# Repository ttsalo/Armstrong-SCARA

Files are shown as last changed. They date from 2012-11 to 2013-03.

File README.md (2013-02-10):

Armstrong, the parallel SCARA 3D printer.

Current version is the A1. It's already capable of printing actual
objects, but is very much in the prototype/alpha stage.

NOTE! The STL files may be out of date at any given time. If you want to
reproduce this, use the SCAD files instead.

Concise contruction instructions:

1. Print plastic parts. You need:
 1 x arm11
 1 x arm12
 1 x arm22
 1 x arm21
 1 x z-carriage
 1 x z-end-bottom
 1 x z-end-top
 1 x z-end-support
 2 x circspline-spline
 2 x circspline-motor-mount
 2 x flexspline
 2 x wave-rotor
 4 x mendel-rod-clamp (from Prusa 2, not included here)
 1 x mendel-coupling (from Prusa 2, the Z rod to motor coupling, not included)

 Everything else except the flexsplines should print fine with 0.25 or 0.3 mm
 layer height. The flexspline should be printed with 0.2 layer height, 2.0
 W/T parameter, one perimeter, no extra perimeters. Retract minimum length
 should be set to 1 mm to force retraction when infilling the teeth. Slic3r
 normally does full infill for the teeth regardless of the infill solidity,
 this is fine.

2. Assemble the arms.
  2.1. Left arm, middle joint, from top down: M8x50 bolt, washer, 608
       bearing, arm11, 608 bearing, washer, arm21, washer, locking nut.
  2.2. Right arm, middle joint, from top down: M8x50 bolt, washer, arm22,
       washer, 608 bearing, arm12, 608 bearing, washer, locking nut.
  2.3. Final (end effector) joint, three times: M4x20 hex key bolt, 
       arm21, 4xwasher, 624 bearing, washer, nut. The 624 bearings should
       run smoothly in the groove of the arm22.

3. Mount arms onto the z-carriage.
  3.1. For each: M8x50 bolt, washer, 608 bearing, flexspline, arm11 or arm12,
       608 bearing, washer, z-carriage, washer, locking nut.

4. Tighten the nuts so that there is no play but the arms move without effort.

5. Insert six M4 nuts in the nut traps of the z-carriage.

6. Place the circsplines on top of the z-carriage (may require some fiddling
   or forcing into place) and check that they mesh with the flexsplines.

7. Mount NEMA17 motors in the motor mounts using M3x8 conical head (sunken)
   screws.

8. Assemble wave drivers. In each end: M4x20 bolt, washer, wave-driver,
   washer, 624 bearing, washer, wave-driver other screw hole, washer,
   locking nut. The wave driver length is critical. The included STLs
   have 52.75 mm total outside dimension. This should work fine at least
   initially. When the drives have been run for some time, wave drivers
   with larger dimensions may be needed (in 0.25 mm increments) to get
   rid of backlash. The drivers are for motors with 20 mm shafts with
   double flats. Other types of motors may need redesigned drivers.

9. Assemble the motor mounts into the z-carriage, 6xM4x20 bolts and washers
   are needed. The wave drivers should insert nicely into the flexsplines
   when the motors are rotated a bit by hand when inserting them.

10. Insert 4xLM8UU linear bearings into the z-carriage, use M3x20 screws
    and nuts for each.

11. Construct the frame. Anything L-shaped and at least 80 mm wide will do.
    Just mount the z-end parts with M8 bolts. If the L-part is sufficiently
    supported, the z-end-support part may be omitted. The height can be
    freely chosen.

12. Mount the 8 mm smooth rods with the bar clamps and M3x24 bolts, nuts
    and washers. Place the z-carriage at the same time and check that it
    travels freely on the rods.

13. Insert a M8 nut into the z-carriage and screw in a M8 threaded rod
    for the Z travel.

14. Mount the Z motor with M3x8 sunken head screws and attach it to the
    M8 threaded rod with the coupling.

15. Place the print bed in the frame. The print area is 200x120, with the
    nearest Y position being 82 mm from the centerline of the arm base
    joints.

16. Mount the extruder. The arms will accept a groove mount extruder
    with small diameter. Tested with J-Head Mk V-b. The mounting bolts
    have the standard 50 mm pattern. (M4 bolts)

17. Do the electrical connections and upload the Marlin SCARA firmware.

18. The printer should now be ready for use.

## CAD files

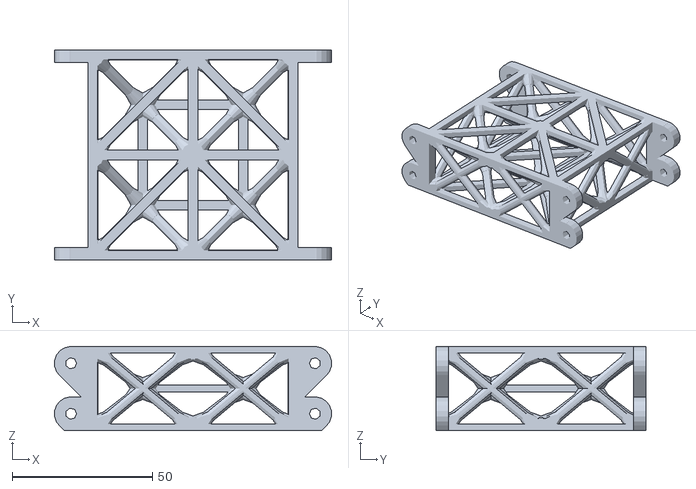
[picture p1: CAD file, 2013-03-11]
frame-bed.stl
98.8 x 75.0 x 30.0

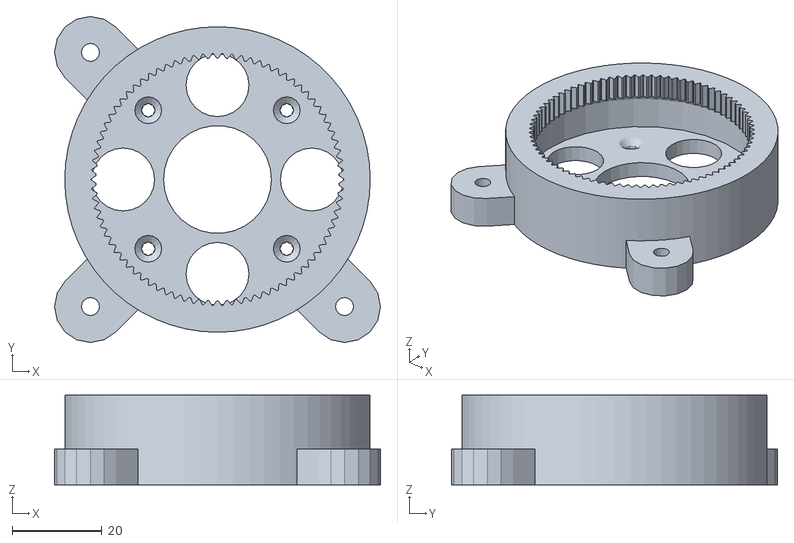
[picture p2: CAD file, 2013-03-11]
circspline.stl
72.6 x 72.6 x 20.0

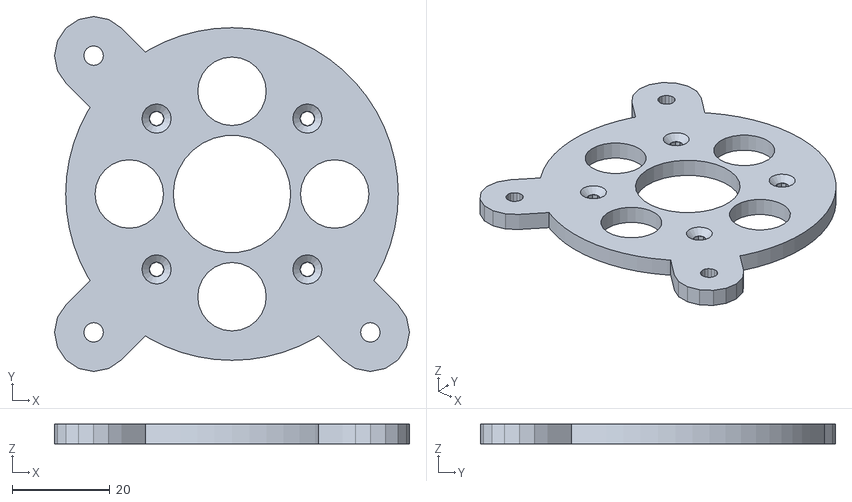
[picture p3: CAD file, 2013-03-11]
circspline-motor-mount.stl
72.6 x 72.6 x 4.00

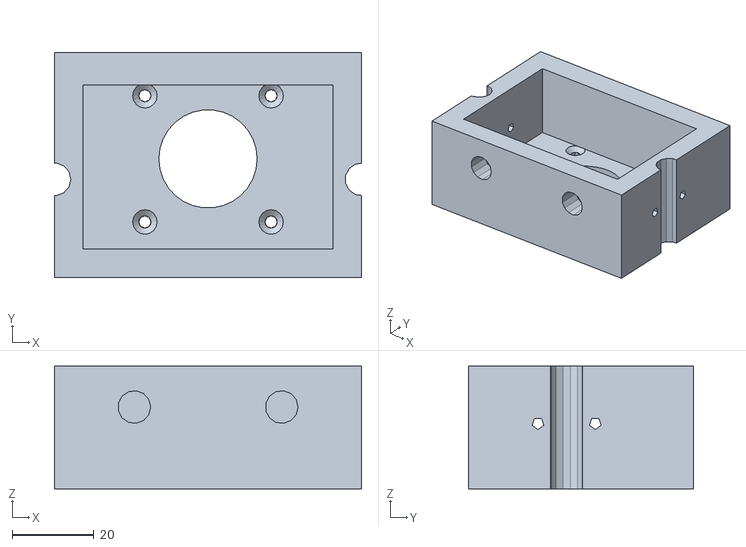
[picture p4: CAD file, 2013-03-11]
z-end-top.stl
75.0 x 55.0 x 30.0

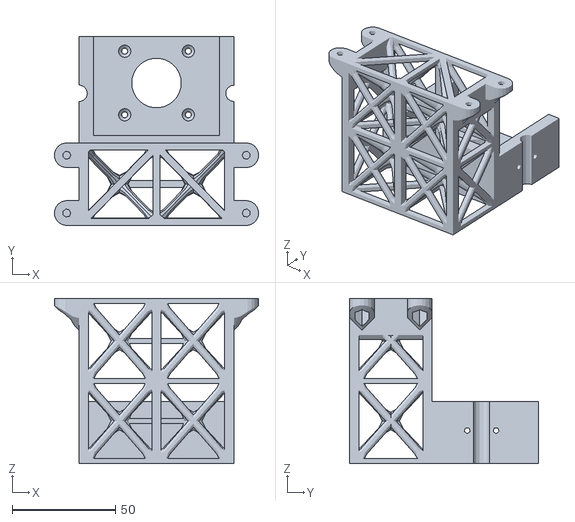
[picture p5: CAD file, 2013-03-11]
frame-top.stl
98.8 x 91.5 x 80.0

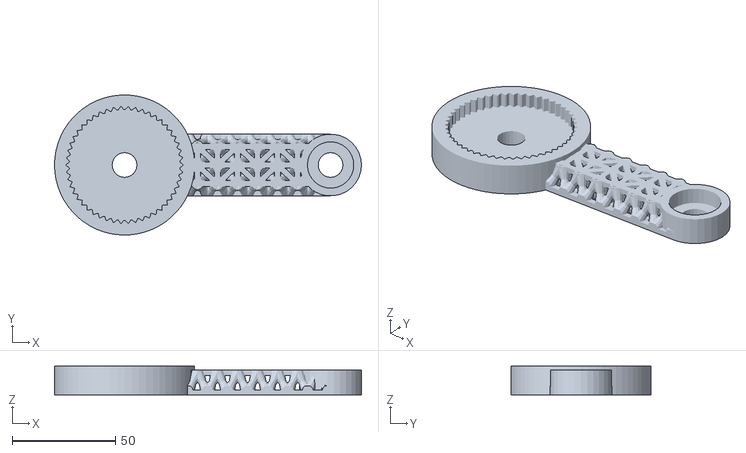
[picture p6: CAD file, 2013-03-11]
arm11.stl
149.0 x 68.0 x 14.0

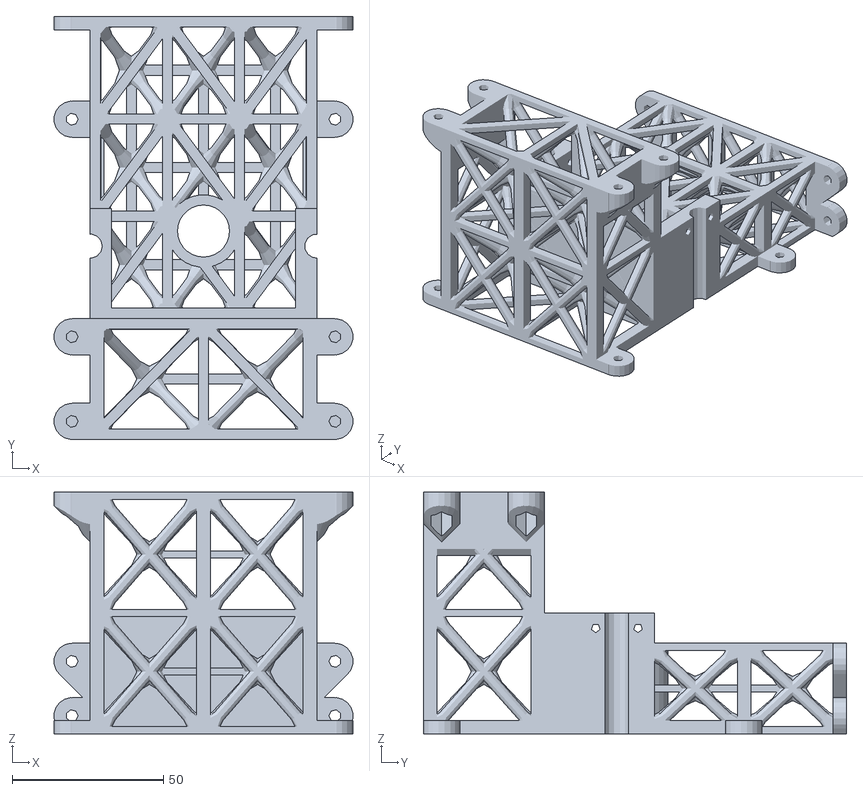
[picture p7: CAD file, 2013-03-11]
frame-bottom.stl
98.8 x 140.0 x 80.0

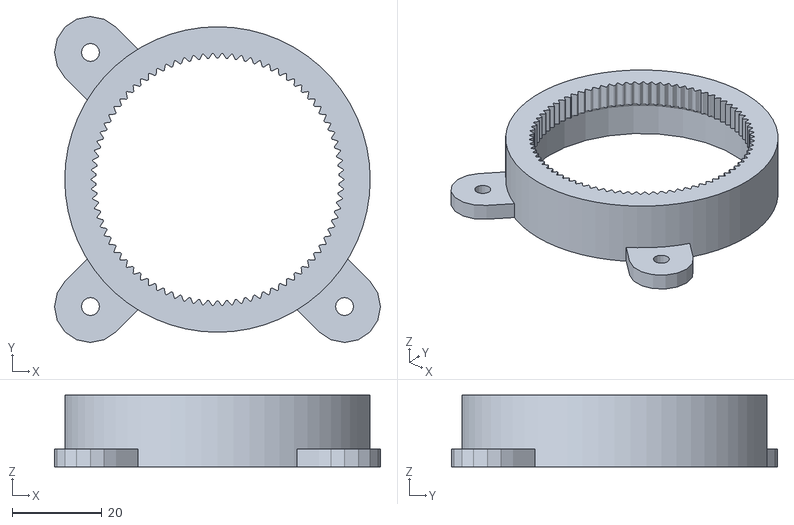
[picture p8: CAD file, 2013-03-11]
circspline-spline.stl
72.6 x 72.6 x 16.0

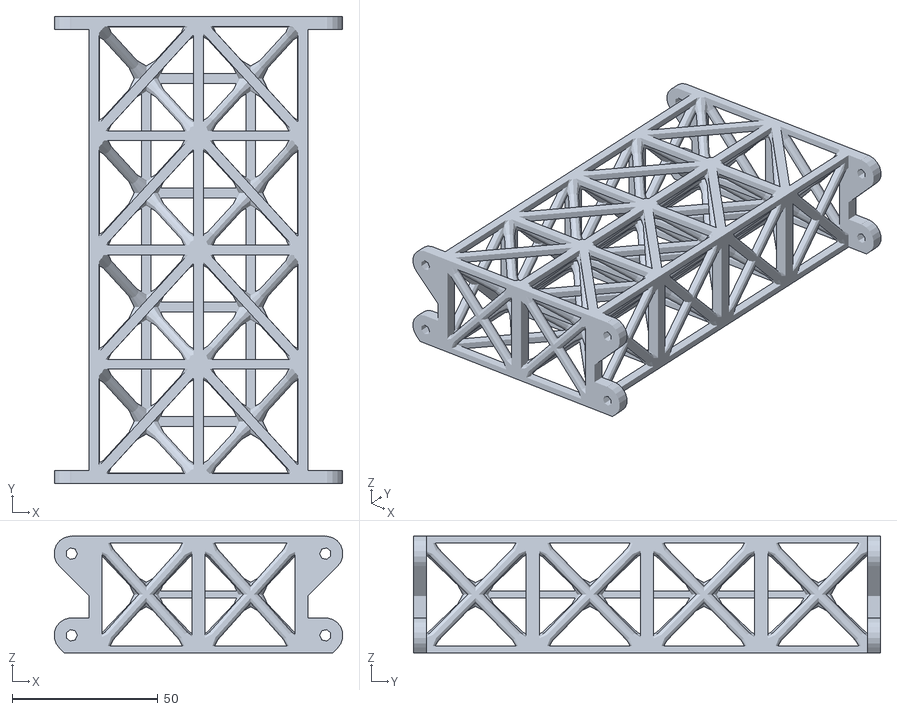
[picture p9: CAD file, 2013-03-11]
frame-extension-double.stl
98.8 x 160.0 x 40.0

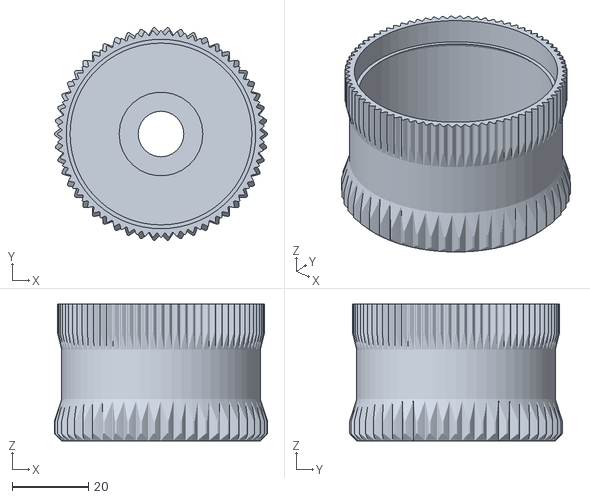
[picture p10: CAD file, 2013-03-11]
flexspline.stl
56.0 x 55.9 x 36.0

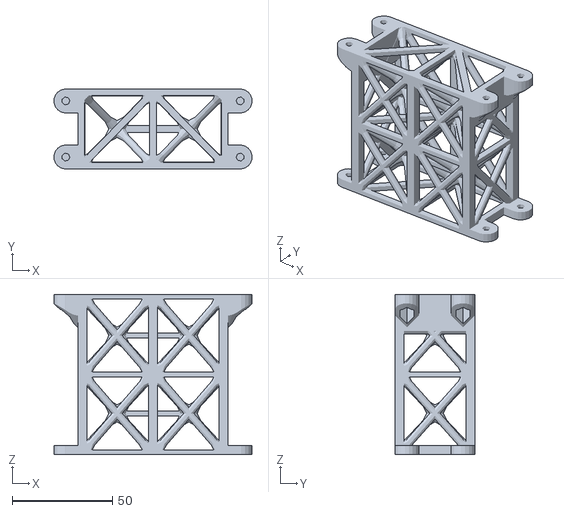
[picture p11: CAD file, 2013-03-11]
frame-extension.stl
98.8 x 40.0 x 80.0

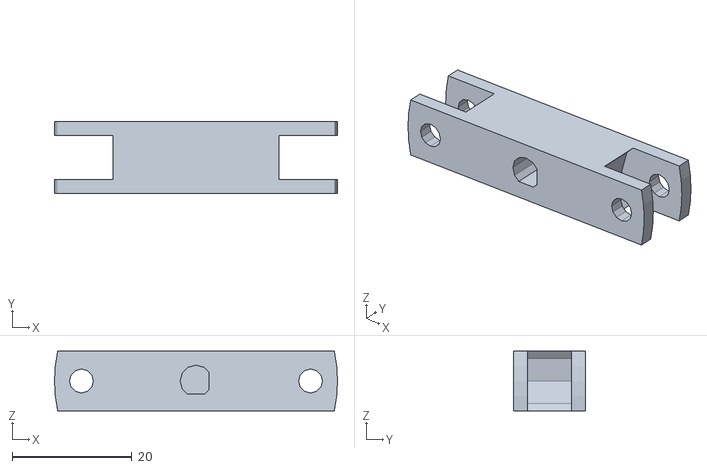
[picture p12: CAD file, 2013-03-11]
wave-rotor.stl
47.2 x 12.0 x 10.0

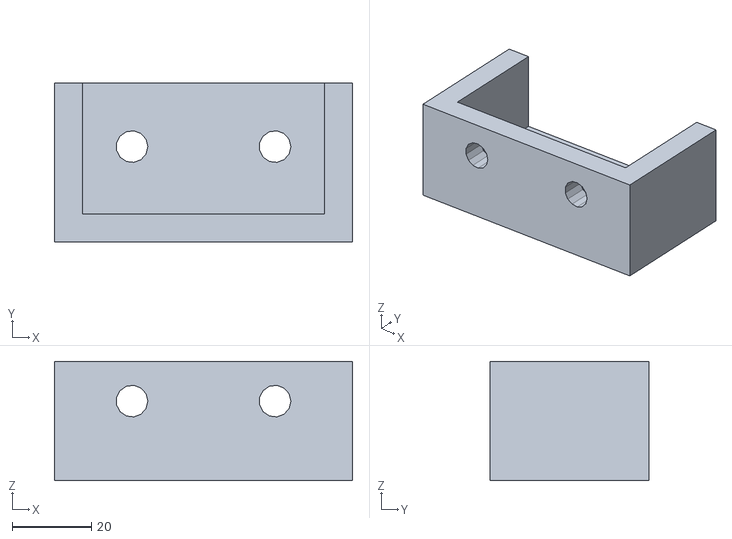
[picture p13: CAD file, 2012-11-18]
z-end-support.stl
75.0 x 40.0 x 30.0

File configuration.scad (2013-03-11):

// Harmonic drive main parameters
press_angle = 35;
flex_teeth = 80;
teeth_diff = 2;

tol = 0.25; // generic tolerance used in some places
lh = 0.3; // layer height needed in a few places

// Main geometry
bearing_r = 22/2;
bearing_h = 7;
washer_h = 1;
bolthead_h = 4;
stepper_shaft_h = 20;
circ_drive_bearing_indent = 1;
flex_bearing_indent = 1;
drive_bearing_r = 13/2;
drive_bearing_h = 7;

// Flexspline dimensions
flex_inner_r = 25.3;
flex_outer_r = 27.6; // was 27.3; // Outer radius clips the teeth peaks, if needed.
flex_h = 36;
flex_bottom_h = 2;
flex_bolthole_r = 6;
flex_bottom_tooth_h = 3; // The height of the straigth part of the bottom teeth
flex_upper_slope_h = 6; // Length of slope from straight part to upper teeth
flex_wt = 0.81; // Wall thickness of the straigt part
flex_extra_upper_wt = 0.4; // Extra wall thickness for the inside of the upper toothed part
flex_lip = 1.4; // Wave driver retaining lip thickness
pitch = 120.5; // Tooth pitch. Tune this to make the tooth valleys line up with the
               // outer surface.
helix_twist = 0; // 3.5;
flex_bottom_teeth = 50;
flex_bottom_pitch = 197;
bottom_press_angle = 40;

// Circspline dimensions
circ_h = 20;
circ_outer_r = 34;
circ_inner_r = 30;
circ_bottom_h = 4;
// Negative clearance cuts a bit from the top of the teeth
circ_tooth_clearance = -0.25;

// Wave driver dimensions
wave_radius = 51.25/2;
driver_h = 12;
driver_w = 10;
driver_tol = 0.15;
drive_bearing_spacing_r = wave_radius - drive_bearing_r;

// The total height of the drive unit, excluding the motor and flexspline base.
assy_h = 50;
stepper_shaft_l = 20;

tooth_overlap = (flex_h + circ_h) - assy_h;

// Position of the middle of the tooth overlap section on the stepper shaft.
stepper_shaft_mid_rot = circ_h - tooth_overlap/2;

echo(str("Tooth overlap: ", tooth_overlap));
echo(str("Drive midpoint on stepper shaft: ", stepper_shaft_mid_rot));

red_r = teeth_diff/flex_teeth;
echo(str("Reduction ratio: 1/", flex_teeth/teeth_diff, " (", red_r, ")"));
echo(str("With 200x16 motor, arc minutes per microstep: ", 360*60/(200*16)*red_r));
echo(str("Linear resolution (mm) for 100 mm arm: ", sin(360/(200*16)*red_r) * 100));
echo(str("Torque (N) at 100 mm for 40 Ncm motor: ", 4/red_r));
echo(str("Linear speed equivalent to standard Prusa's 300 mm/s at 100 mm: ",
         300*80 * sin(360/(200*16)*red_r) * 100));

// Circspline mount dimensions
circ_mount_r = circ_outer_r + 6;
circ_mount_h = 8;
circ_mount_1 = 45;
circ_mount_2 = 135;
circ_mount_3 = 225;

// Master arm height setting
main_arm1_height = 12;
main_arm2_height = 12;

// Arm 1st segment dimensions
arm_flex_base_bottom_h = 8;
arm_flex_base_h = 14;
arm_joint1_base_h = main_arm1_height;
arm_joint1_base_r = 15;
arm_joint1_bearing_indent = 7;
arm_large_bolthole_r=6;
arm_w = 30;
arm1_h = main_arm1_height;

// default length
length = 100;

// New style truss details
truss_z_thickness = 2.5;
truss_xy_thickness = 3.4*(0.25/0.3);
truss_k_thickness = 3.4*(0.25/0.3);
truss_bar_diameter = 3.9*(0.25/0.3);

carr_truss_bar_diameter = 3.25;
carr_truss_thickness = 5;
carr_truss_width_coeff = 0.75;
carr_truss_radius = 0.1;

// Arm 2nd segment dimensions
arm2_h = main_arm2_height;
arm_separation = arm_joint1_base_h - arm_joint1_bearing_indent 
  + bearing_h + washer_h * 2;
arm_bolthole_r=4;
arm_joint2_base_h = main_arm2_height;
arm_joint2_base_r = 15;
arm_joint3_hollow_r = 10;
arm_joint31_base_h = main_arm2_height;
arm_joint31_base_r = 15;
arm_joint31_bearing_r = 13/2;
arm_joint31_bearing_h = 5;
arm_joint31_bearing_clearance = 2;
arm_joint32_base_h = main_arm2_height;
arm_joint32_base_r = 15;
arm_joint32_tube_h_clearance = 1;
arm_joint32_tube_wt = 2;
arm_joint32_tube_groove_depth = 1;
arm_joint31_bearing_spacing = arm_joint3_hollow_r + arm_joint32_tube_wt 
  + arm_joint31_bearing_r;

echo(str("Arm final stage vertical separation: ", arm_separation));
echo(str("Arm final stage total height: ", arm_separation + 2 * arm2_h));

// Default arm lengths
arm1_length = 100;
arm2_length = 150;
arm_spacing = 75;
arm_base_maxrot = 90 - asin((circ_outer_r + arm_w/2) / arm_spacing);
arm_joint_maxrot = 150; // hand-tuned
echo(str("Arm base minimum rotation to clear other base: ", arm_base_maxrot));

// Z carriage dimensions
carr_floor = 1; // Carriage floor thickness.
carr_wt = 3.5; // Carriage wall thickness.
carr_truss_width = arm_spacing + bearing_r * 2 + 20; // 120;
carr_truss_depth = 15;
drive_h = assy_h + bearing_h + washer_h 
  + arm_flex_base_bottom_h; // Total length needed by the drive unit.
carr_truss_length = circ_outer_r + 1 + carr_wt + bearing_r + 10;
carr_rod_offset = -46;
carr_drive_offset = -41;
carr_top_support_thickness = 3;
carr_top_support_width = 14;
carr_top_support_length = 70;

// Z end dimensions
z_end_bottom_thickness = 7;
z_end_bottom_width = arm_spacing + 20;
z_end_bottom_length = 40;
z_end_top_length = 55;
z_end_top_thickness = 7;
z_end_bottom_height = 30;
z_end_top_height = 30;
z_end_rod_offset = 24; // rod center from vertical plate

// Printable area and bed
print_ymin = 82; // Y=0 offset from arm bases (verify by simulation, see demo.scad)
print_xmax = 200;
print_ymin_frame_offset = -carr_rod_offset + z_end_rod_offset + print_ymin;
bed_bolt_r = 2;
bed_bolts = [[100-170/2, 100-124/2, 0], [100-170/2, 100+124/2, 0], [100+170/2, 100, 0]];

echo(str("Print area Y=0 offset from vertical frame: ", print_ymin_frame_offset));

// Frame dimensions
frame_bottom_height = 30;
frame_bottom_length = 100;
frame_back_height = 80;
frame_top_height = 80;
frame_extend_height = 80;
frame_back_depth = 40;
frame_back_width = arm_spacing;

frame_bottom_truss_z_thickness = 2.4;
frame_bottom_truss_xy_thickness = 3.4;
frame_bottom_truss_k_thickness = 3.4;
frame_bottom_truss_bar_diameter = 3.9;
frame_bottom_truss_vert_thickness = 4.5;

frame_back_truss_z_thickness = 2.4;
frame_back_truss_xy_thickness = 3.4;
frame_back_truss_k_thickness = 3.4;
frame_back_truss_bar_diameter = 3.9;
frame_back_truss_vert_thickness = 4.5;

frame_top_truss_z_thickness = 2.4;
frame_top_truss_xy_thickness = 3.4;
frame_top_truss_k_thickness = 3.4;
frame_top_truss_bar_diameter = 3.9;
frame_top_truss_vert_thickness = 4.5;

frame_extend_truss_z_thickness = 2.4;
frame_extend_truss_xy_thickness = 3.4;
frame_extend_truss_k_thickness = 3.4;
frame_extend_truss_bar_diameter = 3.9;
frame_extend_truss_vert_thickness = 4.5;

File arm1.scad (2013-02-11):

include <common.scad>;

module arm1_dummy(length) {
  difference() {
    union() {
      cylinder(r=circ_outer_r, h=arm1_h, $fn=60);
      intersection() {
        cylinder(r=circ_outer_r, h=arm1_h+2, $fn=60);
        translate([0, -arm_w/2, 0])
          cube([length, arm_w, arm1_h+2]);
      }
    }
    translate([0, 0, arm_flex_base_bottom_h]) flexspline_gear(flex_h, -0.4, -0.4);
    cylinder(r=arm_large_bolthole_r, h=arm_flex_base_bottom_h + 1, $fn=24);
    
  }
}

module arm1(length, type, use_truss) {
  difference() {
    union() {
      difference() {
        cylinder(r=circ_outer_r, h=arm_flex_base_h, $fn=60);
      }
      translate([0, -arm_w/2, 0])
        if (use_truss == 0) { cube([length, arm_w, arm1_h]); }
        else { pyramid_box_truss(length, arm_w, arm1_h, 
				 10, 3, 1, truss_z_thickness, truss_xy_thickness, truss_k_thickness,
				 truss_bar_diameter, true, true, 10);
	}
      translate([length, 0, 0]) cylinder(r=arm_joint1_base_r, h=arm_joint1_base_h);
    }
    translate([0, 0, arm_flex_base_bottom_h]) 
      gear(number_of_teeth=flex_bottom_teeth,
	   circular_pitch=flex_bottom_pitch,
	   pressure_angle=bottom_press_angle,
	   clearance = -0.6,
	   gear_thickness = flex_h/2,
	   rim_thickness = flex_h/2,
	   rim_width = 5,
	   hub_thickness = flex_h/2,
	   hub_diameter=0,
	   bore_diameter=0,
	   circles=0,
	   backlash=-0.6,
	   twist=0);
    cylinder(r=arm_large_bolthole_r, h=arm_flex_base_bottom_h + 1, $fn=24);
    if (type == 1) {
      translate([length, 0, 0])
        cylinder(r=arm_large_bolthole_r, h=arm_joint1_base_h + 1, $fn=24);
      translate([length, 0, arm_joint1_base_h-arm_joint1_bearing_indent])
         cylinder(r=bearing_r+tol, h=arm_joint1_bearing_indent + 1);
    } else {
      translate([length, 0, arm_joint1_bearing_indent + lh])
        cylinder(r=arm_large_bolthole_r, h=arm_joint1_base_h + 1, $fn=24);
      translate([length, 0, 0])
         cylinder(r=bearing_r+tol, h=arm_joint1_bearing_indent);
    }
  }
}

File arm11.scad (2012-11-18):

include <arm1.scad>;

arm1(arm1_length, 1, 1);

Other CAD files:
arm12.stl
z-end-bottom.stl
arm12.scad
Armstrong.scad
arm2.scad
arm21.scad
arm22.scad
circspline-motor-mount.scad
circspline-spline.scad
circspline.scad
common.scad
demo.scad
drive-ng.scad
flexspline.scad
frame-bed.scad
frame-bottom.scad
frame-extension-double.scad
frame-extension.scad
frame-top.scad
includes/PyramidSpaceTruss.scad
includes/jonaskuehling-default.scad
includes/lm8uu-holder-slim_double-vertical.scad
includes/parametric_involute_gear_v5.0.scad
wave-rotor.scad
z-carriage.scad
z-end-bottom.scad
z-end-support.scad
z-end-top.scad

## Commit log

2012-11-18 Initial prototype version.
    [Armstrong.scad, SolidReplacementTruss.scad, arm1.scad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]
2012-11-18 Initial prototype prebuilt STLs.
    [arm11.stl, arm12.stl, circspline-motor-mount.stl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]
2012-11-19 Fixed some errors.
    [demo.scad]
2012-11-19 Changed the sloping to improve flexibility and strength.
    [flexspline.scad, flexspline.stl]
2012-11-20 Made the arm flexspline bases and z-carriage main truss, cylindrical walls and LM8UU holders beefier. Should make the main arm axes more rigid to improve print quality.
    [arm1.scad, arm11.stl, arm12.stl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]
2012-11-20 Removed some leftover test code which was messing up the z-carriage.
    [lm8uu-holder-slim_double-vertical.scad, z-carriage.scad]
2012-11-20 Removed accidentally committed temporary file
    [rest.scad]
2012-11-26 Fixed a bug in the flexspline, the bottom teeth were too short after the recent change in the arm drive base thickness.
    [configuration.scad, flexspline.scad, flexspline.stl]
2012-11-28 Tuned the z-carriage wall thicknesses for 0.6 track width, 3 perimeters. Fixed a minor bug in the circspline bolt holes. Reduced the wave driver tolerances to get a tighter fit with the stepper shaft.
    [configuration.scad, lm8uu-holder-slim_double-vertical.scad, wave-rotor.scad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]
2012-11-28 Changed the wave driver rotation for cleaner printability.
    [wave-rotor.scad]
2012-11-28 Regenerated wave driver STL.
    [wave-rotor.stl]
2012-12-21 Changed the splines from herringbones to conventional gear profile. Tuned the tooth profiles, now has 60 teeth with pressure angle of 35. Changed the truss module to pyramid truss structure.
    [PyramidSpaceTruss.scad, arm1.scad, circspline.scad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]
2012-12-22 Fixed the truss generation.
    [PyramidSpaceTruss.scad, arm1.scad]
2013-01-10 Now can create a proper box truss structure.
    [PyramidSpaceTruss.scad]
2013-01-14 The fully rectangular truss section should now be in about the final form.
    [PyramidSpaceTruss.scad]
2013-02-10 Changed the Z-carriage to use the pyramidal truss base.
    [configuration.scad, z-carriage.scad]
2013-02-10 Changed also the second arm segments to use the pyramidal truss.
    [arm1.scad, arm2.scad]
2013-02-10 Superseded by the PyramidSpaceTruss.scad
    [SolidReplacementTruss.scad]
2013-02-11 Fixed the truss generation for arms and z-carriage. Now works correctly with the pyramidal truss module.
    [PyramidSpaceTruss.scad, arm1.scad, arm2.scad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]
2013-02-12 Initial revision of the truss-based frame added.
    [configuration.scad, frame-bottom.scad]
2013-02-12 Added boltholes for the space trusses and added a frame extension piece which utilizes these.
    [PyramidSpaceTruss.scad, common.scad, configuration.scad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]
2013-02-13 Frame bottom and extension pieces now in pretty good shape.
    [PyramidSpaceTruss.scad, configuration.scad, frame-bottom.scad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]
2013-02-13 Added side bolt pattern, cleaned up the indentation
    [PyramidSpaceTruss.scad]
2013-02-13 Added bolt pattern to the front of the bottom part, to attach to the frame bed part.
    [frame-bottom.scad]
2013-02-13 Partial version of the frame bed part.
    [configuration.scad, frame-bed.scad]
2013-02-13 Fixed the cornerbar generation (was doubling the bars in some cases)
    [PyramidSpaceTruss.scad]
2013-02-13 The truss vertical bars were printing a bit flimsy, changed those from round to rectangular. Also added a diaphragm to the upper bolt mounts to help them print cleaner.
    [PyramidSpaceTruss.scad, frame-bottom.scad, frame-extension.scad]
2013-02-15 Truss round bar thickness test.
    [PyramidSpaceTruss.scad]
2013-02-15 Double length frame extension in horizontal print orientation.
    [frame-extension-double.scad]
2013-02-18 Added a truss frame top part.
    [configuration.scad, frame-top.scad]
2013-02-18 Decreased the bottom truss spacing to get a steeper slant in the diagonals.
    [frame-bottom.scad]
2013-02-18 Truss vertical bars now have a separate thickness settings. Also tuned the thicknesses for 0.6 track width printing.
    [configuration.scad]
2013-02-18 New, better material thicknesses for 0.6 track width printing.
    [frame-bottom.scad]
2013-02-18 Better material thicknesses for 0.6 track width printing.
    [PyramidSpaceTruss.scad, frame-extension-double.scad, frame-extension.scad]
2013-02-19 Fixed the thicknesses for the frame top. Some frame bed section development.
    [configuration.scad, frame-bed.scad]
2013-02-19 Frame bed module in prototype form.
    [frame-bed.scad]
2013-03-07 Fixed the frame top generation.
    [frame-top.scad]
2013-03-07 Changed the flexspline back to 0.81 wall thickness (2*0.4 track printing), made the upper tooth slope configurable.
    [configuration.scad, flexspline.scad]
2013-03-07 Dropped the harmonic drive reduction ratio to 40:1, tuned the tooth profiles a bit.
    [configuration.scad]
2013-03-07 Tuned the arm and z-carriage truss parameters a bit.
    [configuration.scad, z-carriage.scad]
2013-03-07 Added new frame parts as build targets
2013-03-07 Still one more tuneup to z-carriage truss parameters.
    [configuration.scad]
2013-03-08 Implemented an extra wall thickness parameter for the upper tooth area of the flexspline and added 0.4 mm of thickness there to add strength to the new, smaller teeth.
    [configuration.scad, flexspline.scad]
2013-03-11 Final version of Armstrong A1
    [arm11.stl, arm12.stl, circspline-motor-mount.stl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]
2013-03-11 Initial revision of the NG drive system
    [drive-ng.scad]
2013-03-11 Basic flange assemblied done
    [drive-ng.scad]
2013-03-12 Minor tuneups for first trial print
    [drive-ng.scad]
2013-03-12 Initial draft of the flexspline
    [drive-ng.scad]
2013-03-20 Flexspline-flange mounting as well as flex side flange bolt holes added.
    [drive-ng.scad]
2013-03-21 Flexspline and flange development
    [drive-ng.scad]
2013-03-21 Tuning, circspline development
    [drive-ng.scad]
2013-03-25 Added 6812 bearing data
    [drive-ng.scad]
